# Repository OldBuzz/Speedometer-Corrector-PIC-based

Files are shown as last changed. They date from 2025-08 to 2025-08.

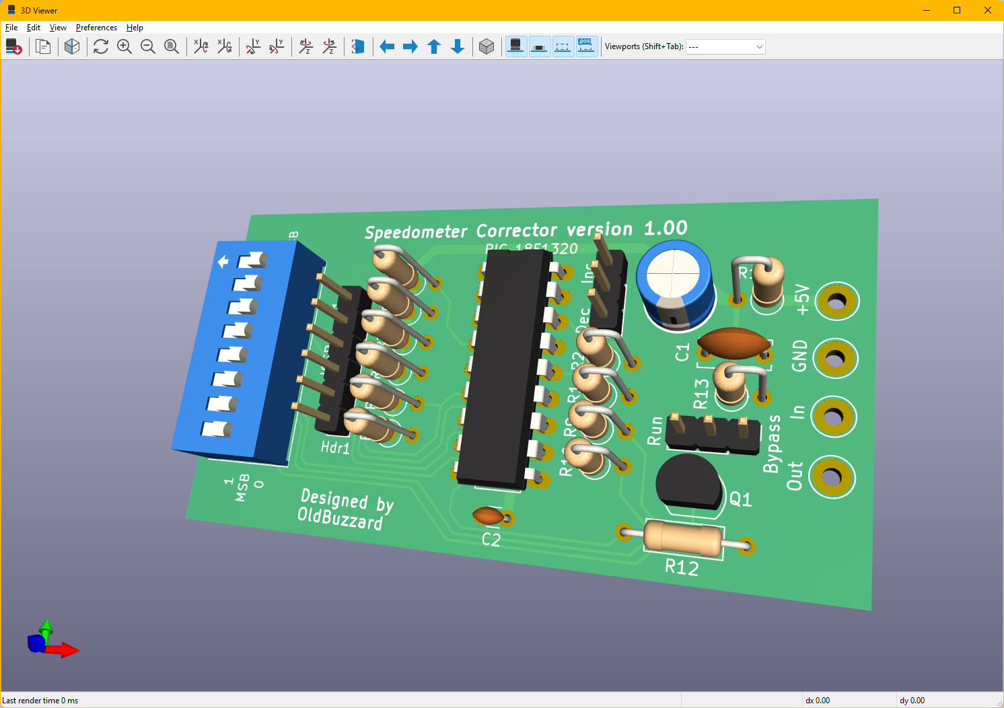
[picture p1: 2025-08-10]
Hardware/KiCad/Images/PCB_07_3D_components.png

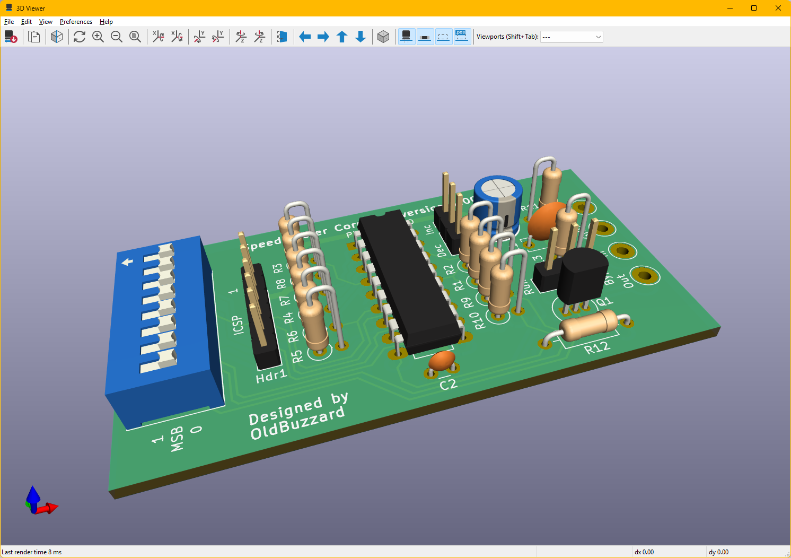
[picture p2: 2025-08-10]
Hardware/KiCad/Images/PCB_06_3D_components.png

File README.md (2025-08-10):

# Speedometer-Corrector-PIC-based
Digital speedometer corrector, based on a PIC 18F1320.

This is a Microchip PIC 18F1320 project for correcting a speedometer when you change tire size or differential gearing. It was initially designed for a Jeep Wrangler TJ (1997-2006). It may also work on other vehicles if they use a 5 volt squarewave signal from the speed sensor to the speedometer or to the PCM/ECU, within the range of 0 Hz to a little over 200 Hz. Some vehicles use a 12 volt speedometer signal, which would require several changes to this circuit to work. Some vehicles may use other signals, like a sinewave, or a CAN bus serial stream. This circuit will not work for those vehicles.

## Important Note

Installing this device involves splicing into your vehicle wiring, and altering the way a sensor reports to the PCM/ECU (engine computer). If you're uncomfortable with doing that, don't. An error could be very costly. It also requires you to burn a program into a PIC microcontroller. If you don't have the equipment to do that, it will cost money and a learning curve to get set up. It's probably not worth it unless you're going to play with other PIC microcontrollers for your own projects. On the other hand, the circuit is simple, with common through-hole parts, and the firmware is short and clean. Calibration is pretty easy.

## How It Works

The Speedo Corrector is a small box which goes between the Vehicle Speed Sensor on your transmission or transfer case and your engine computer (PCM/ECU). It alters the signal to correct for a change in tire diameter or gearing.

First, you take a drive to compare the indicated speed on your speedometer with a GPS speed. You'll do a simple calculation to get a "correction factor", which you'll enter into the Speedo Corrector on a set of 8 switches.

The Speedo Corrector measures the period of the incoming squarewave from the speed sensor, and produces a longer or shorter output squarewave, depending on the correction factor you set.

## License

The firmware is released as Open Source software.
Firmware License: GPL v3

The hardware is released as Open Hardware.
Hardware License: CERN-OHL-S v2

## Hardware

This simple circuit uses common through-hole parts. You can build it on a sea-of-holes proto board, wiring it point-to-point. Or you can make a real PC board, and the KiCad schematic and PCB layout, with Gerber files, is included.

## Firmware

The firmware is pretty short, and is written in C. You'll need the equipment to burn the firmware into the PIC chip.  Microchip MPLAB X IDE v6.20 (free), Microchip XC8 v3.00 compiler (free), Microchip PICkit3 or 4 (costs money) or equivalent.

## Where can I get one?

You'll have to acquire the parts and build it yourself.

## Related Projects

Speedometer Corrector (Arduino-based): An Arduino Pro Mini based speedometer corrector circuit.

https://github.com/OldBuzz/Speedometer-Corrector-Arduino-based

(I previously built an Arduino-based speedometer corrector, based on Tom M'Guinness's design. It works well, and I ran it in my Jeep for over two years.)

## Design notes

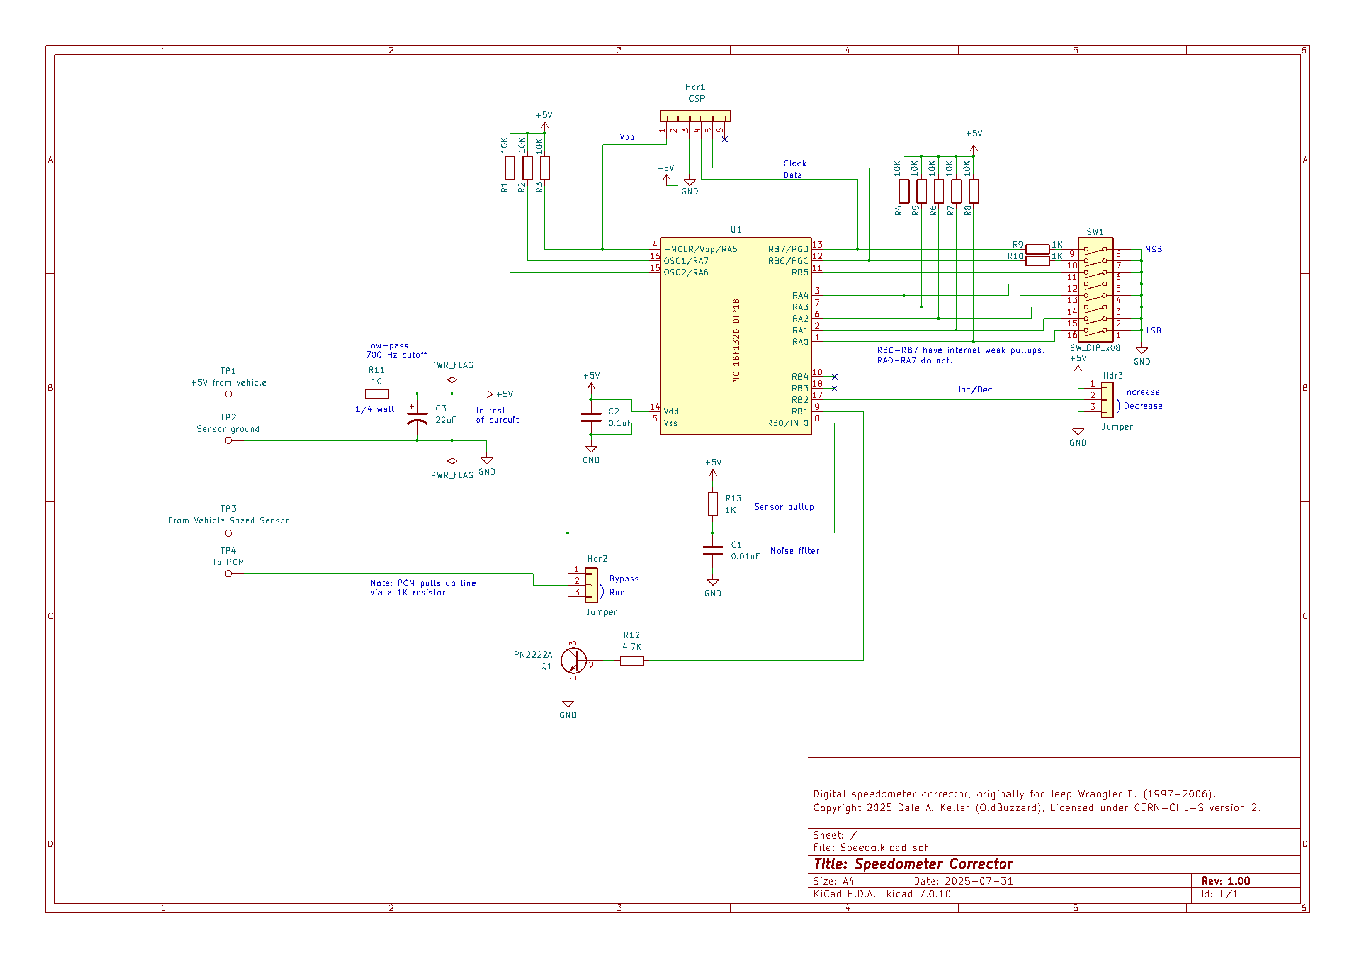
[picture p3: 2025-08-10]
Hardware/KiCad/Images/Speedo_Corrector_schematic.png

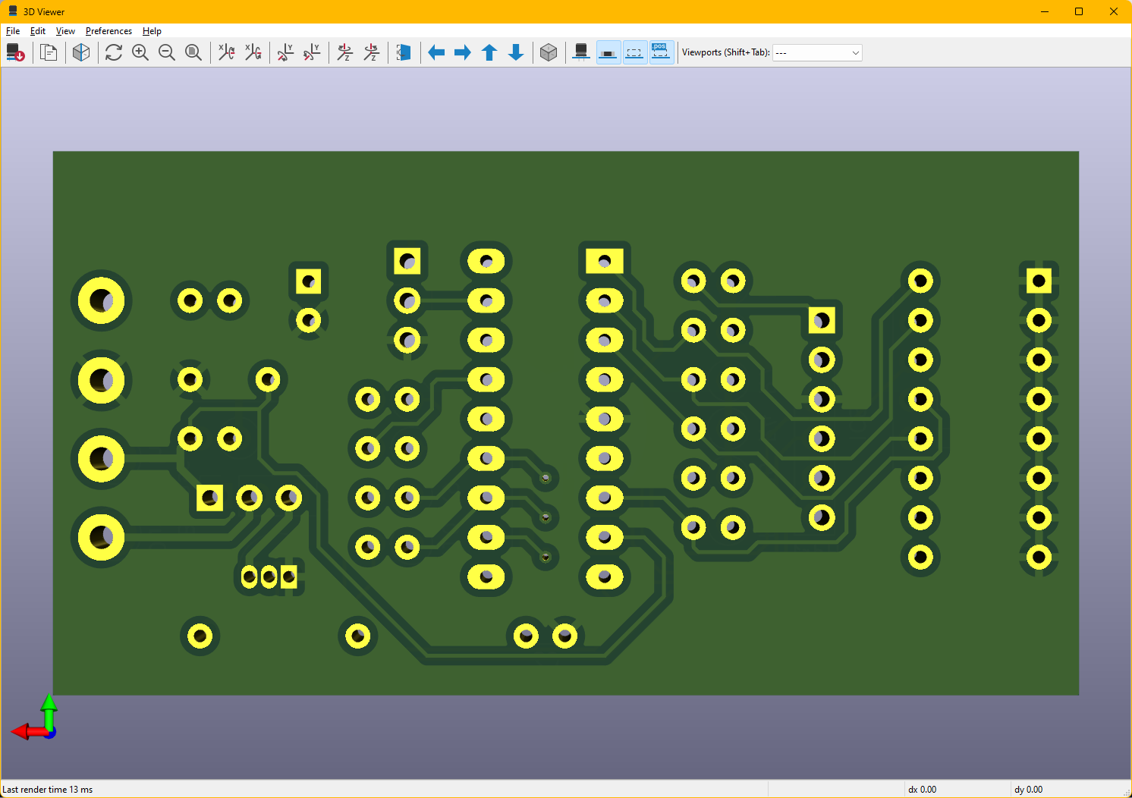
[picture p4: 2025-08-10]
Hardware/KiCad/Images/PCB_05_3D_bottom.png

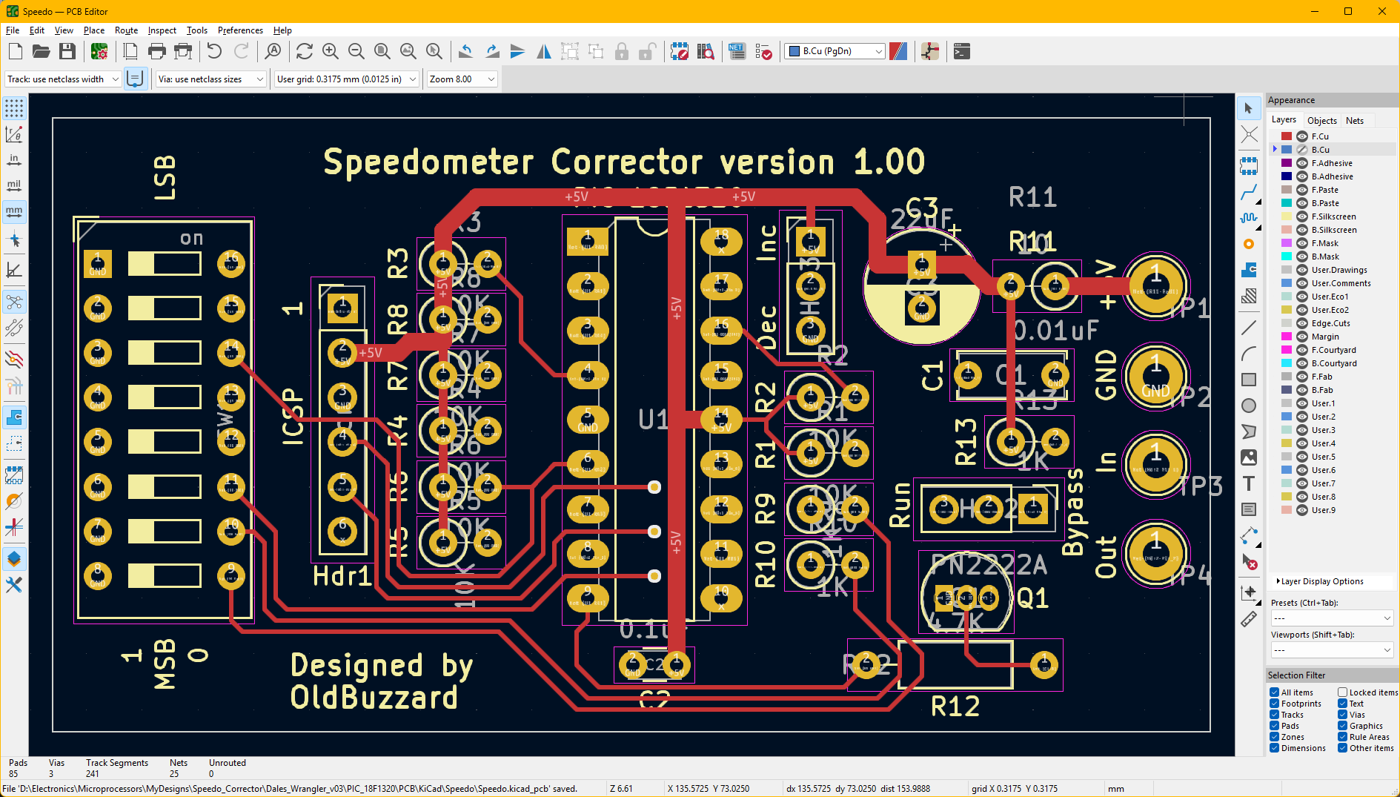
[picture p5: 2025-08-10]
Hardware/KiCad/Images/PCB_01_top.png

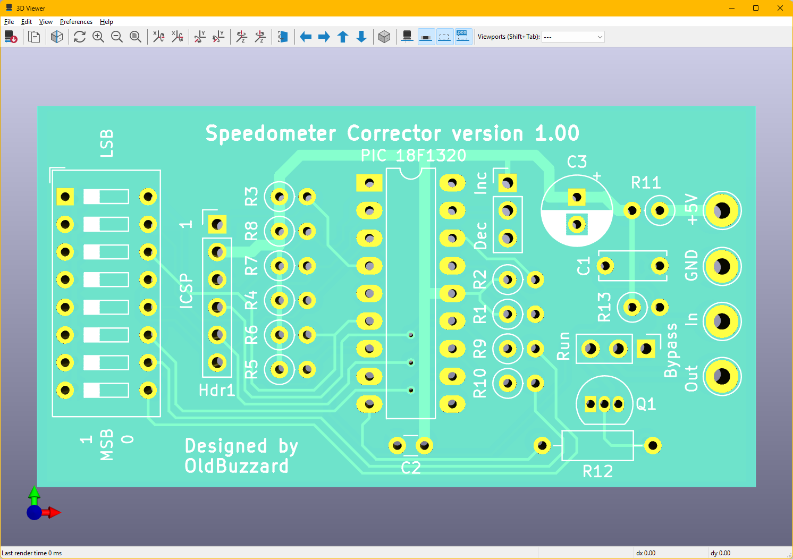
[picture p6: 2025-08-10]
Hardware/KiCad/Images/PCB_04_3D_top.png

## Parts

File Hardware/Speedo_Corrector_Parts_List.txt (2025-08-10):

Speedometer Corrector Parts List
--------------------------------

1   PIC18F1320-E/P (DIP18, extended temperature) microcontroller
1   PN2222A transistor
8   Resistor, 10K, 1/8 to 1/4 watt
1   Resistor, 4.7K, 1/8 to 1/4 watt
3   Resistor, 1K, 1/8 to 1/4 watt
1   Resistor, 10 ohm, 1/4 watt (not lower)
1   Capacitor, 22uF, electrolytic, radial
1   Capacitor, 0.1uF, radial, ceramic disk or MLCC
1   Capacitor, 0.01uF, radial, ceramic disk or MLCC
1   Header, single row, 6 pin (for ICSP)
1   Header, single row, 3 pin (for Inc/Dec)
1   Header, single row, 3 pin (for Run/Bypass)
2   Jumper (for Inc/Dec and Run/Bypass headers)
1   Socket, DIP18 (for PIC)
1   DIP Switch, 8 switches, DIP16 (sand off markings, they'll mislead you)
1   PCB (have one made, or do your own point-to-point)
1   Case (your choice, waterproof, melt-proof)
*   Wires, 18-22 gauge, stranded, four different colors (you choose length)
1   Connector, 4-pin, automotive, waterproof, male (optional)
1   Connector, 4-pin, automotive, waterproof, female (optional)

Many of these can be bought from Mouser or DigiKey:
  https://www.mouser.com
  https://www.digikey.com
Some parts can be found on Amazon (DIP Switch, case, connector) or eBay or
various surplus electronics websites.

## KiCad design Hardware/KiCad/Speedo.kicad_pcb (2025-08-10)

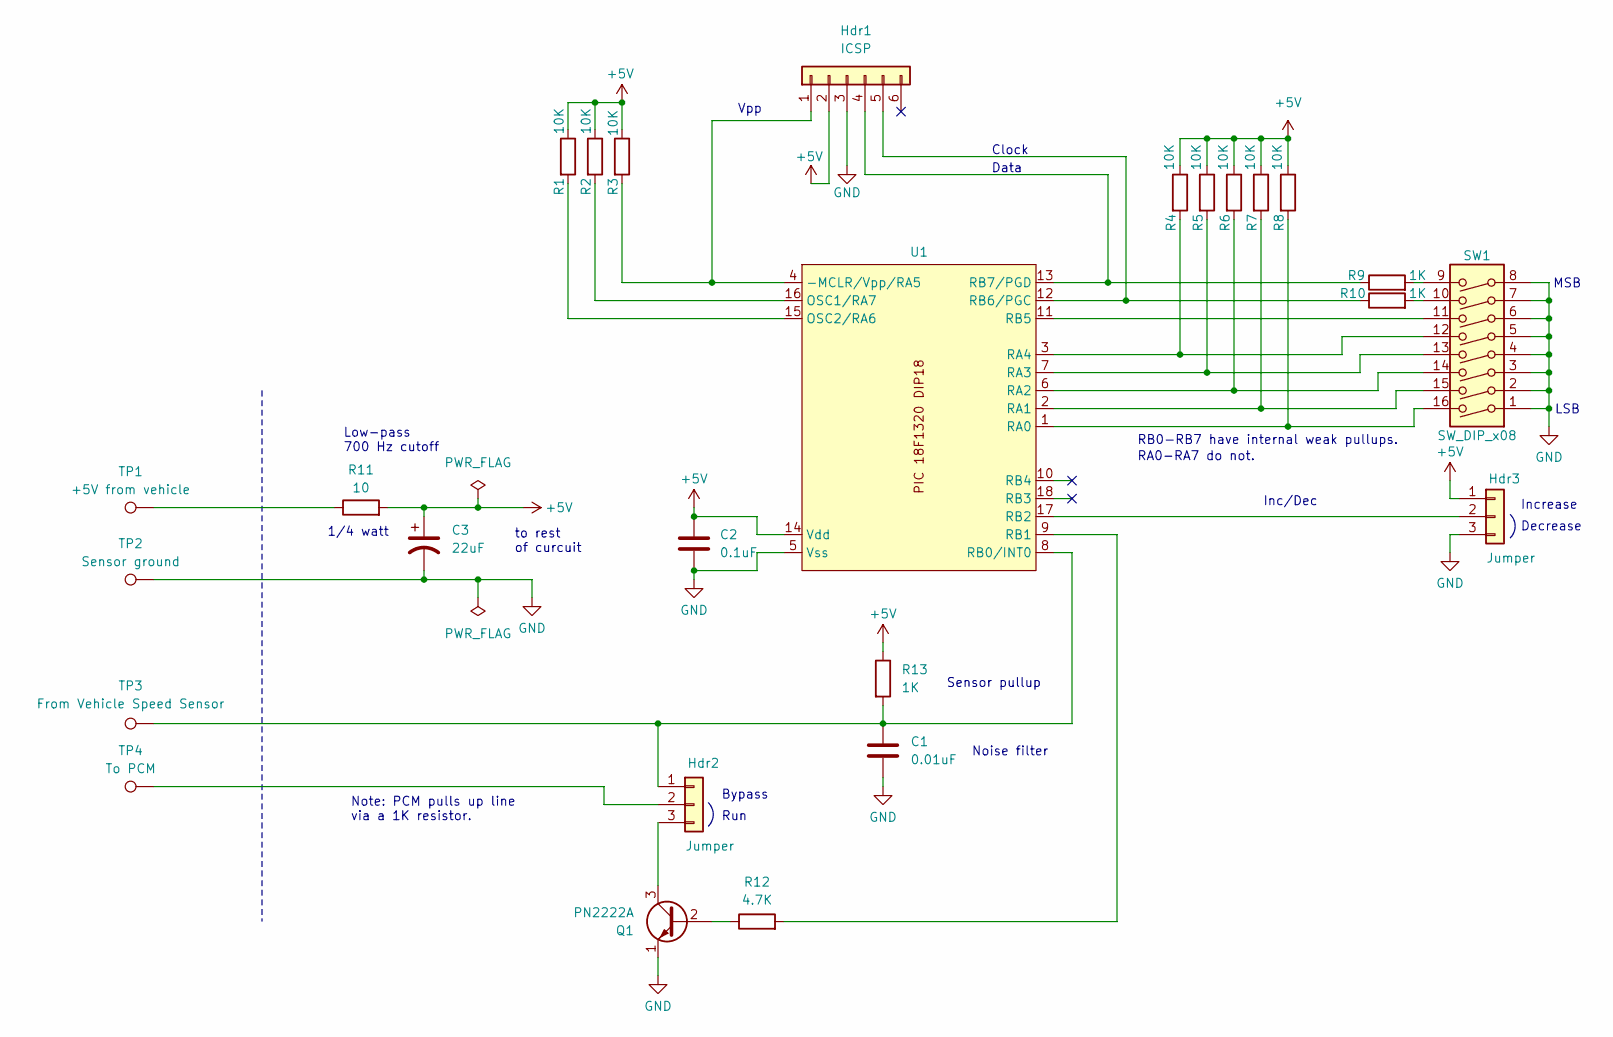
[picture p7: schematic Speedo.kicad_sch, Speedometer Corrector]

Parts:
C1: 0.01uF; C_Disc_D6.0mm_W2.5mm_P5.00mm
C2: 0.1uF; C_Disc_D3.0mm_W1.6mm_P2.50mm
C3: 22uF; CP_Radial_D6.3mm_P2.50mm
Hdr1: ICSP; PinHeader_1x06_P2.54mm_Vertical
Hdr2, Hdr3: Jumper; PinHeader_1x03_P2.54mm_Vertical
Q1: PN2222A; TO-92_Inline
R1, R2, R3, R4, R5, R6, R7, R8: 10K; R_Axial_DIN0207_L6.3mm_D2.5mm_P2.54mm_Vertical
R9, R10, R13: 1K; R_Axial_DIN0207_L6.3mm_D2.5mm_P2.54mm_Vertical
R11: 10; R_Axial_DIN0207_L6.3mm_D2.5mm_P2.54mm_Vertical
R12: 4.7K; R_Axial_DIN0207_L6.3mm_D2.5mm_P10.16mm_Horizontal
SW1: SW_DIP_x08; SW_DIP_SPSTx08_Slide_9.78x22.5mm_W7.62mm_P2.54mm
TP1: +5V from vehicle; TestPoint_THTPad_D3.0mm_Drill1.5mm
TP2: Sensor ground; TestPoint_THTPad_D3.0mm_Drill1.5mm
TP3: From Vehicle Speed Sensor; TestPoint_THTPad_D3.0mm_Drill1.5mm
TP4: To PCM; TestPoint_THTPad_D3.0mm_Drill1.5mm
U1: DIP-18_W7.62mm_LongPads

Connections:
+5V: C2.1, C3.1, Hdr1.2, Hdr3.1, R1.1, R2.1, R3.1, R4.1, R5.1, R6.1, R7.1, R8.1, R11.2, R13.1, U1.14 (Vdd)
GND: C1.2, C2.2, C3.2, Hdr1.3, Hdr3.3, Q1.1 (E), SW1.1, SW1.2, SW1.3, SW1.4, SW1.5, SW1.6, SW1.7, SW1.8, TP2.1, U1.5 (Vss)
unnamed: Hdr1.1, R3.2, U1.4 (-MCLR/Vpp/RA5)
unnamed: Hdr1.4, R9.1, U1.13 (RB7/PGD)
unnamed: Hdr1.5, R10.1, U1.12 (RB6/PGC)
unnamed: C1.1, Hdr2.1, R13.2, TP3.1, U1.8 (RB0/INT0)
unnamed: Hdr2.2, TP4.1
unnamed: Hdr2.3, Q1.3 (C)
unnamed: Hdr3.2, U1.17 (RB2)
unnamed: Q1.2 (B), R12.1
unnamed: R9.2, SW1.9
unnamed: R10.2, SW1.10
unnamed: R11.1, TP1.1
unnamed: R2.2, U1.16 (OSC1/RA7)
unnamed: R1.2, U1.15 (OSC2/RA6)
unnamed: R8.2, SW1.16, U1.1 (RA0)
unnamed: R7.2, SW1.15, U1.2 (RA1)
unnamed: R6.2, SW1.14, U1.6 (RA2)
unnamed: R5.2, SW1.13, U1.7 (RA3)
unnamed: R4.2, SW1.12, U1.3 (RA4)
unnamed: R12.2, U1.9 (RB1)
unnamed: SW1.11, U1.11 (RB5)

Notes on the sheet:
1/4 watt
Increase
Bypass
Decrease
RB0-RB7 have internal weak pullups.
Clock
Noise filter
to rest of curcuit
Sensor pullup
Run
MSB
RA0-RA7 do not.
Vpp
Low-pass 700 Hz cutoff
Data
LSB
Inc/Dec
Note: PCM pulls up line via a 1K resistor.

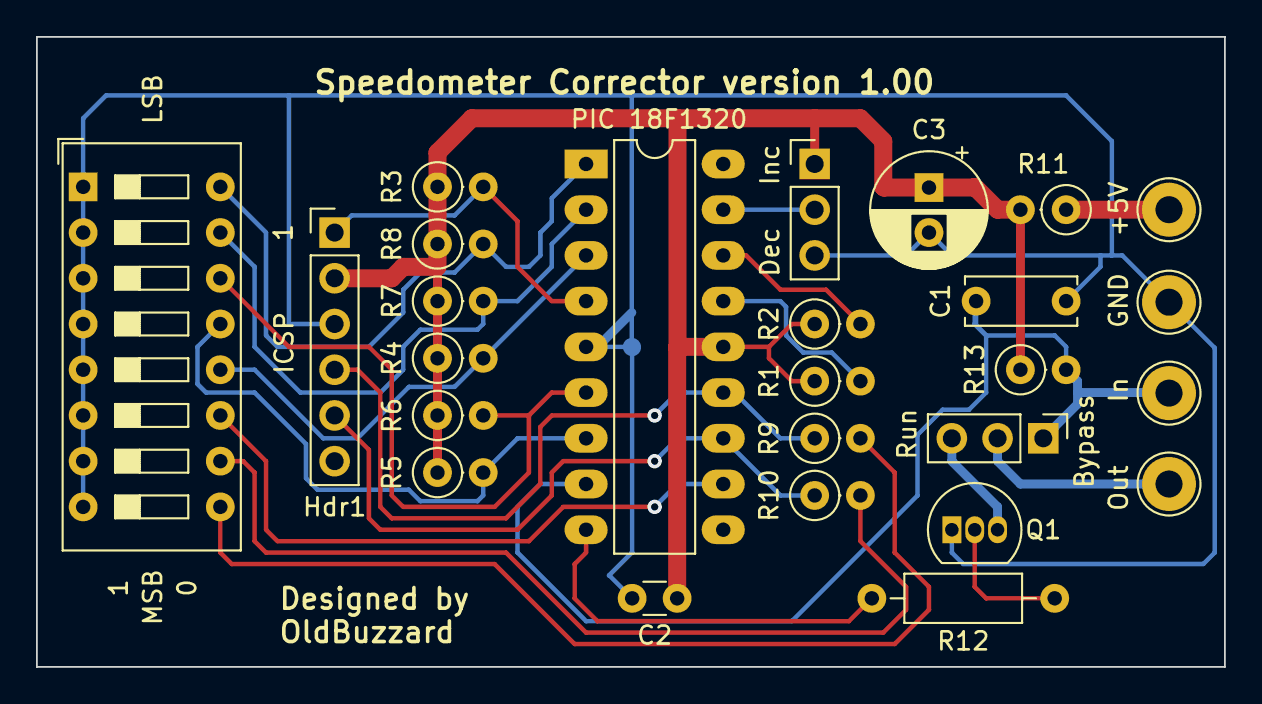
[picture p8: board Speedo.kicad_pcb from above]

Board: 2 copper layers, 66.0 x 35.0 mm, 26 parts (0 on the bottom side), 22 nets.

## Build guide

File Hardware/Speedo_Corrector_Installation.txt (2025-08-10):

Speedometer Corrector Installation
----------------------------------

-------------
Installing It
-------------
You'll have to provide a case for the PCB. The usual mounting location is under
the hood, up high on the firewall, so a sturdy waterproof and melt-proof case
should be used. Alternately, you can mount it in the cab under the dash, if you
drill a hole in the firewall to feed wires through. These options will splice
into the vehicle wiring in the engine compartment on the firewall. Or you can
run a wire from near the speed sensor on the transfer case (with automotive
connectors instead of splicing), up through the tunnel under the console, to a
spot under the driver seat.

If you wire it at the firewall, you'll have to splice into the wiring from the
PCM (ECU) to the speed sensor on the transmission or transfer case. You'll need
to identify the speed sensor power (+5V), ground, and signal wires. You can
find that information in a Factory Service Manual. See the "Jeep" folder. It
might be a good idea to add a 4-pin waterproof connector so you can easily
disconnect the Speedo Corrector if needed.

If you wire it at the transfer case, you can use a couple of OEM style 3-pin
connectors and avoid splicing into the wiring. Those connectors are fairly
pricy, and you'll need a high quality crimper.

The +5V and GND wires must still go to the speed sensor, so you'll have to tee
the wires to get the same feeds into the Speedo Corrector. The signal wire must
be cut. The signal coming up from the speed sensor goes into one pad on the
Speedo Corrector, and the modified signal comes out of another pad and goes on
to the PCM (ECU).

Set the Inc/Dec jumper appropriately, per the Calibration document. Set the 8
switches for the percentage of change, too. Set the Run/Bypass jumper to Run.

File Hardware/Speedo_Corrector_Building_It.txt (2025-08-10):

Building the Speedometer Corrector
----------------------------------

-----------
Building It
-----------
A KiCad project is provided, with schematic and PC board layout. The Gerber
files can be sent to a PCB manufacturer for professionally done boards. Most
American companies will cost a lot for 3 boards, plus shipping. Most Chinese
companies will cost a tiny fraction of the American cost, for 10 boards, plus
higher shipping, plus a possible import duty/tariff. A duty or tariff can cost
more than the PCBs. Or you can wire it up by hand on a sea-of-holes breadboard.
The project uses common easy-to-get parts (Mouser or DigiKey will have
everything, maybe eBay or Amazon for an affordable 8-switch DIP). You could
even design your own board for surface mount components, to shrink it, although
the 8-switch DIP and the two jumpers and the ICSP header limit how small you
can go.

You will need a Microchip PIC 18F1320-E/P (extended temperature) 18-pin DIP
through-hole microcontroller, programmed with the firmware provided here. You
can program the chip in a stand-alone programmer, or use a PICkit 3 or 4 or
equivalent device to program it on the board via ICSP. It can be compiled and
burned with Microchip MPLAB X IDE v6.20, Microchip XC8 v3.00 compiler,
Microchip PICkit3.

The DIP-switch must be oriented correctly in the board (which will probably
look wrong). See the "Photos" folder. Holding the circuit board vertically with
the switch location up, the switch should go into the board with the "ON" side
down, with pin 1 at the upper right. Once soldered in place, the markings on
the DIP-switch should be sanded off to avoid confusion. The 1-8 switches are
now bit 0-7, and the "ON" side is now zero, and the "OFF" side is now one. An
open switch (off) allows the PIC to pull the signal up, and a closed switch
(on) pulls the signal to ground, hence the inverted logic.

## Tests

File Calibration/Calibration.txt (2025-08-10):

Speedometer Corrector Calibration
---------------------------------

Speedometers, from the factory, are usually off a little, usually reading a
little higher than your actual speed. A manufacturer wouldn't want any lawsuits
from people getting speeding tickets because the speedometer says 50 when
you're doing 53. And if you change your tire size or your gearing, your
speedometer will be farther off, too high or too low.

-----------
Gather Data
-----------
Do this before installing the Speedo Corrector, or with it installed and
jumpered for Bypass. Drive the vehicle, preferably on a flat straight highway,
with little traffic, at a fairly high speed (a very steady 60 to 75 MPH). Write
down the speedometer reading, and a GPS reading. Take multiple readings, a
dozen or so, since they'll vary a little. An assistant is almost essential.

---------------------------
Calculate Correction Factor
---------------------------
Average all of the speedometer readings together, and average all of the GPS
readings together.

If the speedometer readings are lower than the GPS readings, you'll need an
Increase (to the Speedo). Otherwise you'll need a Decrease.

Divide the higher number by the lower, and subtract 1, and multiply by 200.
For example: You get a speedometer reading of 60, and a GPS reading of 53.3.
So you're going to need a Decrease, because you want to decrease the indicated
speed on the speedometer. Divide the higher number, 60, by the lower, 53.3,
and get 1.1257. Subtract 1 giving 0.1257. Multiply by 200 giving 25.14. Round
that to the nearest whole number giving 25. That's your correction factor.

----------------
Set DIP Switches
----------------
Set the Inc/Dec jumper to Increase or Decrease.

There are 8 switches on the DIP-switch. The left-most switch is the most
significant bit, and the right-most switch is the least significant bit.

The 8 switches get the binary value of the correction factor you calculated
above. Windows has a handy calculator with a Programmer option in the menu.
Type in your value (like 25 from the example above), and it will show
you the binary value (00011001). If it only shows four digits, tack '0000' on
in front of it to get eight digits. Enter that binary number on the 8 switches
(switch up for 1, down for 0). Our example setting would be Decrease 25.
(that's actually 25 / 2 = 12.5%)

Set the Run/Bypass jumper to Run.

-------------------
Drive, Check, Tweak
-------------------
Go for a test drive with your helper. Check the speedometer against a GPS
again.

Your speedometer should now be correct, or close. You might need to tweak it a
little. Use the calculator to find the binary numbers on either side of your
calculated calibration factor, and set the switches accordingly.

Note: The device only loads the calibration factor at power-up, so if you're
changing the switches with the vehicle running, you'll have to power-cycle the
device.

If the speedometer is still way off, something is wrong, and you'll need to
troubleshoot.

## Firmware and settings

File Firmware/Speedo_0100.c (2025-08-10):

/*-----------------------------------------------------------------------------

 Speedo_0100.c

 Speedometer Corrector
 Originally for Jeep Wrangler TJ (1997-2006)

 MCU: PIC 18F1320
 Using this particular PIC for its two 16-bit timers, and the ability to clock
 those timers at an appropriate rate without using a crystal.

 Input pin: RB0/INT0 (pin 8) (has a Schmitt Trigger input for INT0)
 Output pin: RB1 (pin 9)
 Switch pins: RA0-RA4 and RB5-RB7 (pins 1, 2, 6, 7, 3, 11, 12, 13)
 Inc/Dec pin: RB2 (pin 17)

 Version:
  01.00  2025/07/30  First "real" version.

 Copyright 2025 Dale A. Keller (OldBuzzard)

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
-----------------------------------------------------------------------------*/

/*-----------------------------------------------------------------------------
 #pragma config statements should precede project file includes.
 Use project enums instead of #define for ON and OFF.
-----------------------------------------------------------------------------*/

// CONFIG1H
#pragma config OSC = INTIO2     // Oscillator Selection bits (Internal RC oscillator, port function on RA6 and port function on RA7)
#pragma config FSCM = OFF       // Fail-Safe Clock Monitor Enable bit (Fail-Safe Clock Monitor disabled)
#pragma config IESO = OFF       // Internal External Switchover bit (Internal External Switchover mode disabled)

// CONFIG2L
#pragma config PWRT = OFF       // Power-up Timer Enable bit (PWRT disabled)
#pragma config BOR = OFF        // Brown-out Reset Enable bit (Brown-out Reset disabled)
// BORV = No Setting

// CONFIG2H
#pragma config WDT = OFF        // Watchdog Timer Enable bit (WDT disabled (control is placed on the SWDTEN bit))
#pragma config WDTPS = 1024     // Watchdog Timer Postscale Select bits (1:1024)

// CONFIG3H
#pragma config MCLRE = OFF      // MCLR Pin Enable bit (RA5 input pin enabled, MCLR disabled)

// CONFIG4L
#pragma config STVR = ON        // Stack Full/Underflow Reset Enable bit (Stack full/underflow will cause Reset)
#pragma config LVP = OFF        // Low-Voltage ICSP Enable bit (Low-Voltage ICSP disabled)

// CONFIG5L
#pragma config CP0 = OFF        // Code Protection bit (Block 0 (00200-000FFFh) not code-protected)
#pragma config CP1 = OFF        // Code Protection bit (Block 1 (001000-001FFFh) not code-protected)

// CONFIG5H
#pragma config CPB = OFF        // Boot Block Code Protection bit (Boot Block (000000-0001FFh) not code-protected)
#pragma config CPD = OFF        // Data EEPROM Code Protection bit (Data EEPROM not code-protected)

// CONFIG6L
#pragma config WRT0 = OFF       // Write Protection bit (Block 0 (00200-000FFFh) not write-protected)
#pragma config WRT1 = OFF       // Write Protection bit (Block 1 (001000-001FFFh) not write-protected)

// CONFIG6H
#pragma config WRTC = OFF       // Configuration Register Write Protection bit (Configuration registers (300000-3000FFh) not write-protected)
#pragma config WRTB = OFF       // Boot Block Write Protection bit (Boot Block (000000-0001FFh) not write-protected)
#pragma config WRTD = OFF       // Data EEPROM Write Protection bit (Data EEPROM not write-protected)

// CONFIG7L
#pragma config EBTR0 = OFF      // Table Read Protection bit (Block 0 (00200-000FFFh) not protected from table reads executed in other blocks)
#pragma config EBTR1 = OFF      // Table Read Protection bit (Block 1 (001000-001FFFh) not protected from table reads executed in other blocks)

// CONFIG7H
#pragma config EBTRB = OFF      // Boot Block Table Read Protection bit (Boot Block (000000-0001FFh) not protected from table reads executed in other blocks)

/*-----------------------------------------------------------------------------
 Includes and Defines
-----------------------------------------------------------------------------*/
#include <xc.h>                 // Pulls in the device header for your PIC.
#include <stdbool.h>            // true & false defined here

#define _XTAL_FREQ 2000000      // 2 MHz

/*-----------------------------------------------------------------------------
 Global variables
-----------------------------------------------------------------------------*/
volatile unsigned int   inTicks;        // 16-bit
volatile unsigned int   tmrTicks;       // 16-bit
volatile unsigned int   calFactor;      // 16-bit
volatile _Bool          inInt;          // flag showing input int occurred
volatile _Bool          T1overflow;     // T1 overflow semaphore
volatile _Bool          T1overflow2;    // T1 second overflow semaphore

/*-----------------------------------------------------------------------------
 Initialization
-----------------------------------------------------------------------------*/
void init(void) {
    unsigned int iAmount = 0;   // amount to increase or decrease

    // set up internal oscillator prescaler
    OSCCON = 0b01011110;    // IDLEN=0, IRCF=2MHz, OSTS=1, IOFS=1, SCS=10
    
    // disable analog input (disabled at reset, but ports are analog - dumb)
    ADCON0bits.ADON = 0;    // disable A/D convertor
    ADCON1 = 0b01111111;    // set RA0, RA1, RA2, RA3 and RB0, RB1, RB4 to
                            //   digital, not analog

    // RA0-RA7 input (no pull-ups available)
    TRISA = 0b11111111;

    // RB0 input, RB1 output, RB2-7 input (with weak pull-ups)
    TRISB = 0b11111101;     // RB1 output, all others input
    RBPU = 0;               // RBPU (INTCON2 bit 7) enable all B pull-ups

    // set up Timer1
    T1CON = 0b10110000;     // 16-bit R/W, 1:8 prescale, Fosc/4, disabled
    PIE1bits.TMR1IE = 1;    // enable Timer1 interrupt (overflow)
    PIR1bits.TMR1IF = 0;    // clear Timer1 interrupt flag
    T1overflow = true;      // T1 overflow semaphore
    T1overflow2 = true;     // T1 second overflow semaphore

    // set up Timer3
    T3CON = 0b10110000;         // 16-bit R/W, 1:8 prescale, Fosc/4, disabled
    PIE2bits.TMR3IE = 1;        // enable Timer3 interrupt
    PIR2bits.TMR3IF = 0;        // clear Timer3 interrupt flag

    // set up INT0 on RB0
    INTCONbits.INT0IE = 1;      // enable INT0 on RB0 (always high priority)
    INTCON2bits.INTEDG0 = 0;    // set INT0 to falling edge
    INTCONbits.INT0IF = 0;      // clear INT0 flag

    // set up priority interrupts
    RCONbits.IPEN = 1;          // enable priority interrupts
                                // INT0 interrupts are always high priority
    IPR1bits.TMR1IP = 0;        // set Timer1 interrupt to low priority
    IPR2bits.TMR3IP = 0;        // set Timer3 interrupt to low priority

    // read switches (5 switches on port A and 3 switches on port B)
    //   this 8-bit number represents 2 * percentage (0-99%) so we can get
    //   1/2 percent increments
    iAmount = (PORTA & 0b00011111) | (PORTB & 0b11100000);
    if(iAmount > 199u) iAmount = 199u;  // set a limit (99.5%)

    // read Inc/Dec jumper, set calibration factor
    if(PORTBbits.RB2) {             // if RB2 is high, increase
        calFactor = 200u - iAmount; // smaller number = higher frequency
    } else {                        // else decrease
        calFactor = 200u + iAmount; // larger number = lower frequency
    }

    // clear "input int occurred" flag
    inInt = false;

    // init tmrTicks for Timer 3 (full 16-bit count, ~1 rollover per second,
    //   ~2 seconds per full cycle, ~1/8 MPH)
    tmrTicks = 0;

    WDTCONbits.SWDTEN = 1;          // enable watchdog timer

    WRITETIMER1(0);                 // clear timer 1
    T1CONbits.TMR1ON = 1;           // start Timer1

    WRITETIMER3(0);                 // clear timer 3
    T3CONbits.TMR3ON = 1;           // start Timer3

    INTCONbits.GIEH = 1;            // enable high global interrupts
    INTCONbits.GIEL = 1;            // enable low global interrupts
}

/*-----------------------------------------------------------------------------
 Interrupt (HIGH priority)

 Interrupt from RB0/INT0 falling edge (in pin 8 from speed sensor, full wave).
-----------------------------------------------------------------------------*/
void __interrupt(high_priority) highISR(void) {
    // INT0 occurs on the falling edge of the speed squarewave input
    if (INTCONbits.INT0IF) {        // if interrupt flag is set:
        if (!T1overflow2) {         // if T1 has not overflowed,
            inTicks = READTIMER1(); // get Timer 1 count (full input cycle)
            inInt = true;           // set flag that input int occurred
            T1overflow = false;     // clear semaphore
        }
        WRITETIMER1(0);             // clear Timer 1
        T1overflow2 = false;        // clear second semaphore
        INTCONbits.INT0IF = 0;      // clear RB0/INT0 interrupt flag
    }
}

/*-----------------------------------------------------------------------------
 Interrupt (LOW priority)

 Interrupt from Timer1 overflow (vehicle very slow or stopped).
 Interrupt from Timer3 overflow (an output half wave has completed).
-----------------------------------------------------------------------------*/
void __interrupt(low_priority) lowISR(void) {
    // T1 overflows if vehicle is extremely slow or stopped
    if (PIR1bits.TMR1IF) {          // if T1 overflow interrupt flag is set:
        T1overflow = true;          // set semaphore
        T1overflow2 = true;         // set second semaphore
        PIR1bits.TMR1IF = 0;        // clear Timer 1 overflow interrupt flag
    }
    // T3 overflows when an output half cycle has completed
    if (PIR2bits.TMR3IF) {          // if T3 overflow interrupt flag is set:
        if (!T1overflow)            // if T1 has not overflowed,
            LATBbits.LATB1 = ~LATBbits.LATB1; // toggle output pin (RB1 pin 9)
        WRITETIMER3(tmrTicks);      // write value to Timer 3
        PIR2bits.TMR3IF = 0;        // clear Timer 3 overflow interrupt flag
    }
}

/*-----------------------------------------------------------------------------
 Main
-----------------------------------------------------------------------------*/
void main(void) {
    unsigned int i, outTicks;

    init(); // do initialization
    
    while(1) {
        if (inInt) {
            // calculate half-cycle time, and scale it
            INTCONbits.GIEH = 0;        // disable high global interrupts
            i = inTicks;                // quick copy
            INTCONbits.GIEH = 1;        // enable high global interrupts
            outTicks = (unsigned int)(((unsigned long)(i >> 1u) *
                       (unsigned long)calFactor) / 200u);

            // calculate next half-cycle timer value
            i = 65535u - outTicks;
            INTCONbits.GIEL = 0;        // disable low global interrupts
            tmrTicks = i;               // quick copy
            INTCONbits.GIEL = 1;        // enable low global interrupts

            // clear "input int occurred" flag
            inInt = false;
        }

        CLRWDT();                       // kick the dog
    }
    
    return; // never happens
}

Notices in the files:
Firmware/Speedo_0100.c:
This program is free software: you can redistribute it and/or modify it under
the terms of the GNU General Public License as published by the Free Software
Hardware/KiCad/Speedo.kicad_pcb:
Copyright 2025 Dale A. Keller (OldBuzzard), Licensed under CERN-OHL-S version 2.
